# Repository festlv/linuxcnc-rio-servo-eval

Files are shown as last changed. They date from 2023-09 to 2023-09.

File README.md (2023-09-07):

# LinuxCNC-RIO evaluation/prototype board

This repository contains a quick&dirty board to evaluate feasibility of using [LinuxCNC-RIO](https://github.com/multigcs/LinuxCNC-RIO) for analog servo motor control.
The board is designed as an addon for [Colorlight i5](https://tomverbeure.github.io/2021/01/22/The-Colorlight-i5-as-FPGA-development-board.html) development board. 

Design contains:
* +/-10V analog output (from pwmdir input) + 24V enable output
* differential step/dir + single ended 24V enable output
* differential encoder input on DB9 connector (RS422) with index pulse. Pinout for Ditron DC10 linear scale.
* 4 single ended 24V inputs (limit switches, EStop)
* +24V input, +5V, +/- 15V outputs for development board and analog output.

__N.B.__: There is no isolation present on the board, it relies on the Ethernet isolation alone!

## Current state

The design is not verified in real hardware yet, proceed with caution. Some aspects of the design were simulated in LTSpice, see `ltspice/`

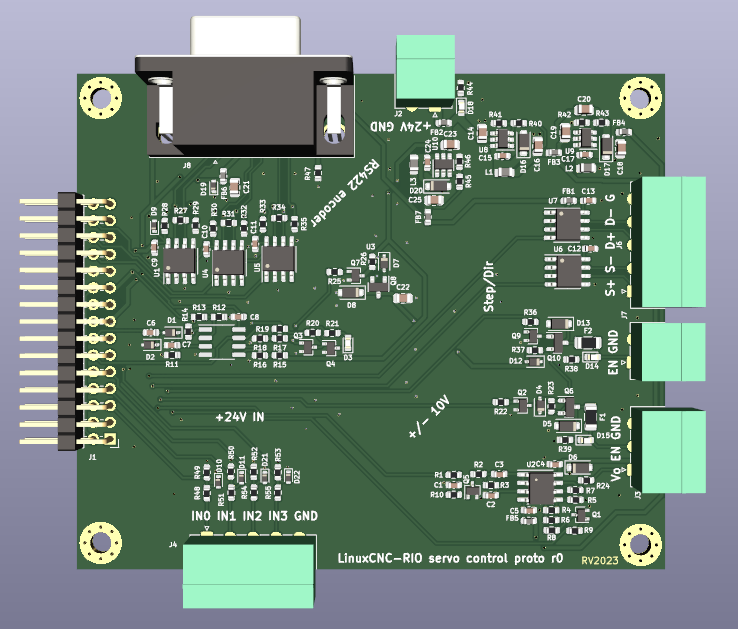
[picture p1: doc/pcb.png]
3d render of the pcb


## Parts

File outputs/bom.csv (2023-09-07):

Source: | /home/reinis/personal/cnc/colorlight-cnc-proto/colorlight-cnc-proto.kicad_sch
Date: | Thu 07 Sep 2023 10:59:34 AM EEST
Tool: | Eeschema 7.0.7
Generator: | /usr/share/kicad/plugins/bom_csv_grouped_by_value.py
Component Count: | 141
Collated Components:
Item | Qty | Reference(s) | Value | LibPart | Footprint | Datasheet | DNP | LCSC# | MPN | Manufacturer
1 | 1 | C1 | 3.3nF | Device:C_Small | Capacitor_SMD:C_0603_1608Metric | ~
2 | 1 | C2 | 220pF | Device:C_Small | Capacitor_SMD:C_0603_1608Metric | ~
3 | 1 | C3 | 680pF | Device:C_Small | Capacitor_SMD:C_0603_1608Metric | ~
4 | 12 | C4, C5, C6, C8, C9, C10, C11, C12, C13, C15, C17, C24 | 0.1uF | Device:C_Small | Capacitor_SMD:C_0603_1608Metric | ~
5 | 1 | C7 | 1uF | Device:C_Small | Capacitor_SMD:C_0603_1608Metric | ~
6 | 9 | C14, C16, C18, C19, C20, C21, C22, C23, C25 | 10uF | Device:C_Small | Capacitor_SMD:C_0805_2012Metric | ~ |  | C440198 | GRM21BR61H106KE43L
7 | 2 | D1, D2 | BAT54WS | hadv-diodes:BAT54WS | Diode_SMD:D_SOD-323 | https://datasheet.lcsc.com/lcsc/2206271801_FUXINSEMI-BAT54WS_C3040452.pdf |  | C3040452 | BAT54WS | Fuxinsemi
8 | 3 | D3, D14, D15 | LED_RED | hadv-ui:LED_RED | LED_SMD:LED_0603_1608Metric | ~ |  | C434419 | SZYY0603R | Yongyu Photoelectric
9 | 3 | D4, D7, D12 | BZT52C10S | hadv-diodes:BZT52C10S | Diode_SMD:D_SOD-323 | ~ |  | C5270769 | BZT52C10S | YFW
10 | 3 | D5, D8, D13 | SMF24A | hadv-protection:SMF24A | Diode_SMD:D_SOD-123F | https://datasheet.lcsc.com/lcsc/2304140030_Shandong-Jingdao-Microelectronics-SMF24A_C169430.pdf |  | C169430 | SMF24A | Shandong Jingdao Microelectronics
11 | 1 | D6 | SMF10CA | hadv-protection:SMF10CA | Diode_SMD:D_SOD-123F | https://www.littelfuse.com/~/media/electronics/datasheets/tvs_diode_arrays/littelfuse_tvs_diode_array_sd_c_datasheet.pdf.pdf |  | C5310922 | SMF10CA | Sunmate
12 | 5 | D9, D10, D11, D21, D22 | BSD5C031V | hadv-protection:BSD5C031V | Diode_SMD:D_SOD-523 | https://datasheet.lcsc.com/lcsc/1912111437_BORN-BSD5C031V_C151984.pdf |  | C151984 | BSD5C031V | BORN
13 | 3 | D16, D17, D20 | DSS34 | hadv-diodes:DSS34 | Diode_SMD:D_SOD-123F | https://datasheet.lcsc.com/lcsc/2004141809_BORN-DSS34_C511866.pdf |  | C511866 | DSS34 | BORN
14 | 1 | D18 | LED_GREEN | hadv-ui:LED_GREEN | LED_SMD:LED_0603_1608Metric | ~ |  | C434423 | SZYY0603YG | Yongyu Photoelectric
15 | 1 | D19 | PESD5V0S1BBN | hadv-protection:PESD5V0S1BBN | Diode_SMD:D_SOD-523 | https://datasheet.lcsc.com/lcsc/1912111437_BORN-PESD5V0S1BBN_C314264.pdf |  | C314264 | PESD5V0S1BBN | BORN
16 | 2 | F1, F2 | BSMD1206-100-24V | hadv-protection:BSMD1206-100-24V | Fuse:Fuse_1206_3216Metric | ~ |  | C910830 | BSMD1206-100-24V | BHFUSE
17 | 7 | FB1, FB2, FB3, FB4, FB5, FB6, FB7 | FB_100R_3A | hadv-passives:FB_100R_3A | Inductor_SMD:L_0603_1608Metric | ~ |  | C96995 | UPZ1608E101-3R0TF | Sunlord
18 | 1 | J1 | Conn_02x15_Odd_Even | Connector_Generic:Conn_02x15_Odd_Even | Connector_PinHeader_2.54mm:PinHeader_2x15_P2.54mm_Horizontal | ~ |  | C2894995
19 | 2 | J2, J7 | TERM-BLK-2H | hadv-connectors:TERM-BLK-2H | Connector_Phoenix_MC:PhoenixContact_MC_1,5_2-G-3.5_1x02_P3.50mm_Horizontal | ~ |  | C441171 | KF2EDGR-3.5-2P | Cixi Kefa Elec
20 | 1 | J3 | TERM-BLK-3H | hadv-connectors:TERM-BLK-3H | Connector_Phoenix_MC:PhoenixContact_MC_1,5_3-G-3.5_1x03_P3.50mm_Horizontal | ~ |  | C441172 | KF2EDGR-3.5-3P | Cixi Kefa Elec
21 | 2 | J4, J6 | TERM-BLK-5H | hadv-connectors:TERM-BLK-5H | Connector_Phoenix_MC:PhoenixContact_MC_1,5_5-G-3.5_1x05_P3.50mm_Horizontal | ~ |  | C441174 | KF2EDGR-3.5-5P | Cixi Kefa Elec
22 | 1 | J8 | DB9_Receptacle | hadv-connectors:DB9_Receptacle | Connector_Dsub:DSUB-9_Female_Horizontal_P2.77x2.84mm_EdgePinOffset7.70mm_Housed_MountingHolesOffset9.12mm | ~ |  | C141882 | D-DMR009PF-D002 | Ckmtw
23 | 3 | L1, L2, L3 | MLP2012S4R7MT0S1 | hadv-inductors:MLP2012S4R7MT0S1 | Inductor_SMD:L_0805_2012Metric | ~ |  | C87543 | MLP2012S4R7MT0S1 | TDK
24 | 7 | Q1, Q2, Q3, Q4, Q5, Q7, Q9 | BSS138W | hadv-transistors:BSS138W | Package_TO_SOT_SMD:SOT-323_SC-70 | ~ |  | C504052 | BSS138W | Jiangsu Changjing Electronics Technology Co., Ltd.
25 | 3 | Q6, Q8, Q10 | AO3401A | hadv-transistors:AO3401A | Package_TO_SOT_SMD:SOT-23 | http://www.vishay.com/docs/70209/70209.pdf |  | C347476 | AO3401A | UMW
26 | 29 | R1, R4, R5, R6, R9, R10, R14, R15, R17, R18, R19, R20, R22, R23, R25, R26, R36, R37, R38, R39, R44, R48, R49, R50, R51, R52, R53, R54, R55 | 10K | Device:R_Small | Resistor_SMD:R_0603_1608Metric | ~
27 | 1 | R2 | 150K | Device:R_Small | Resistor_SMD:R_0603_1608Metric | ~
28 | 3 | R3, R11, R13 | 47K | Device:R_Small | Resistor_SMD:R_0603_1608Metric | ~
29 | 1 | R7 | 70K | Device:R_Small | Resistor_SMD:R_0603_1608Metric | ~
30 | 1 | R8 | 5.83K | Device:R_Small | Resistor_SMD:R_0603_1608Metric | ~
31 | 1 | R12 | 100K | Device:R_Small | Resistor_SMD:R_0603_1608Metric | ~
32 | 8 | R16, R21, R28, R29, R30, R32, R33, R35 | 1K | Device:R_Small | Resistor_SMD:R_0603_1608Metric | ~
33 | 1 | R24 | 10R | Device:R_Small | Resistor_SMD:R_0603_1608Metric | ~
34 | 3 | R27, R31, R34 | 120R | Device:R_Small | Resistor_SMD:R_0603_1608Metric | ~
35 | 2 | R40, R42 | 510K | Device:R_Small | Resistor_SMD:R_0603_1608Metric | ~
36 | 2 | R41, R43 | 30K | Device:R_Small | Resistor_SMD:R_0603_1608Metric | ~
37 | 1 | R45 | 82K | Device:R_Small | Resistor_SMD:R_0603_1608Metric | ~
38 | 1 | R46 | 16K | Device:R_Small | Resistor_SMD:R_0603_1608Metric | ~
39 | 1 | R47 | 0R | Device:R_Small | Resistor_SMD:R_0603_1608Metric | ~
40 | 5 | U1, U4, U5, U6, U7 | CS48505S | hadv-interface:CS48505S | Package_SO:SOIC-8_3.9x4.9mm_P1.27mm | https://datasheet.lcsc.com/lcsc/2207041730_Chipanalog-CS48505S_C3202824.pdf |  | C3202824 | CS48505S | Chipanalog
41 | 1 | U2 | LM358DT | hadv-opamps:LM358DT | Package_SO:SO-8_3.9x4.9mm_P1.27mm | http://www.ti.com/lit/ds/symlink/lm2904-n.pdf |  | C9418 | LM358DT | STMicroelectronics
42 | 1 | U3 | LM2903 | hadv-opamps:LM393 | Package_SO:SOP-8_3.76x4.96mm_P1.27mm | http://www.ti.com/lit/ds/symlink/lm393.pdf |  | C400839 | LM393 | IDCHIP
43 | 3 | U8, U9, U10 | LGS5145 | hadv-vregs:LGS5145 | Package_TO_SOT_SMD:SOT-23-6 | https://datasheet.lcsc.com/lcsc/2304071600_Legend-Si-LGS5145_C5123971.pdf |  | C5123971 | LGS5145

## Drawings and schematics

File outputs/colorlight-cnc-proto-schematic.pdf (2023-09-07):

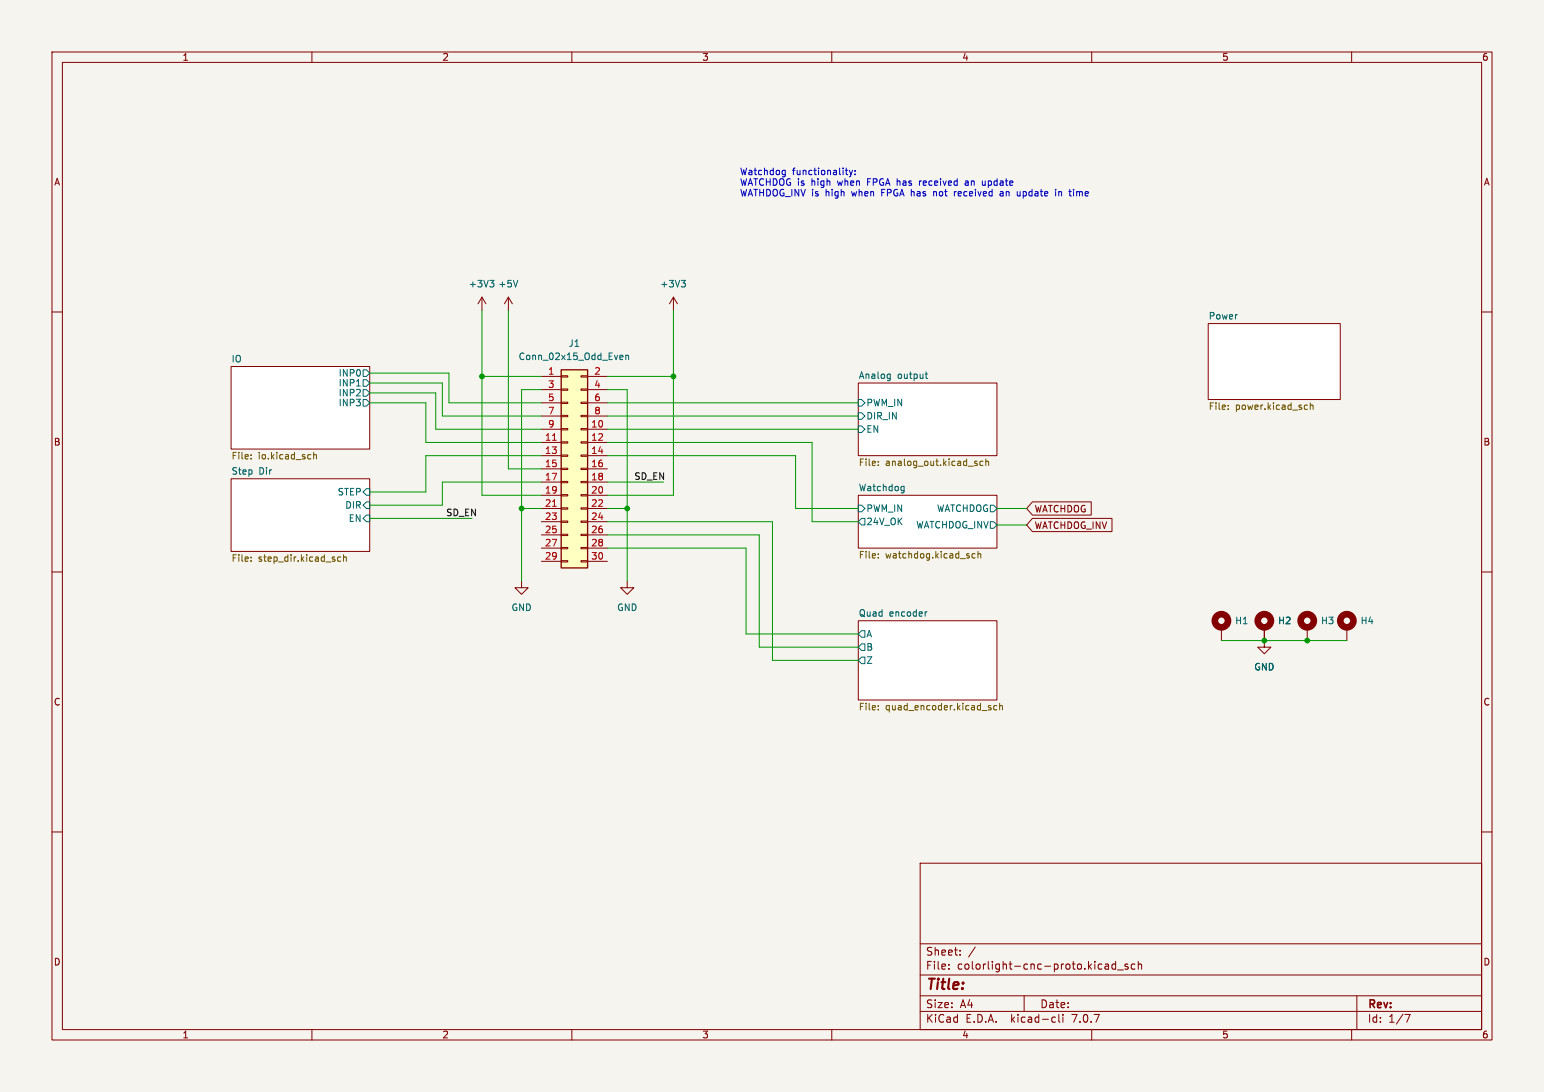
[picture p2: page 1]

9 | | 10
11 | | 12
13 | | 14

Id: 1/7 Title: File: colorlight-cnc-proto.kicad_sch Sheet: /

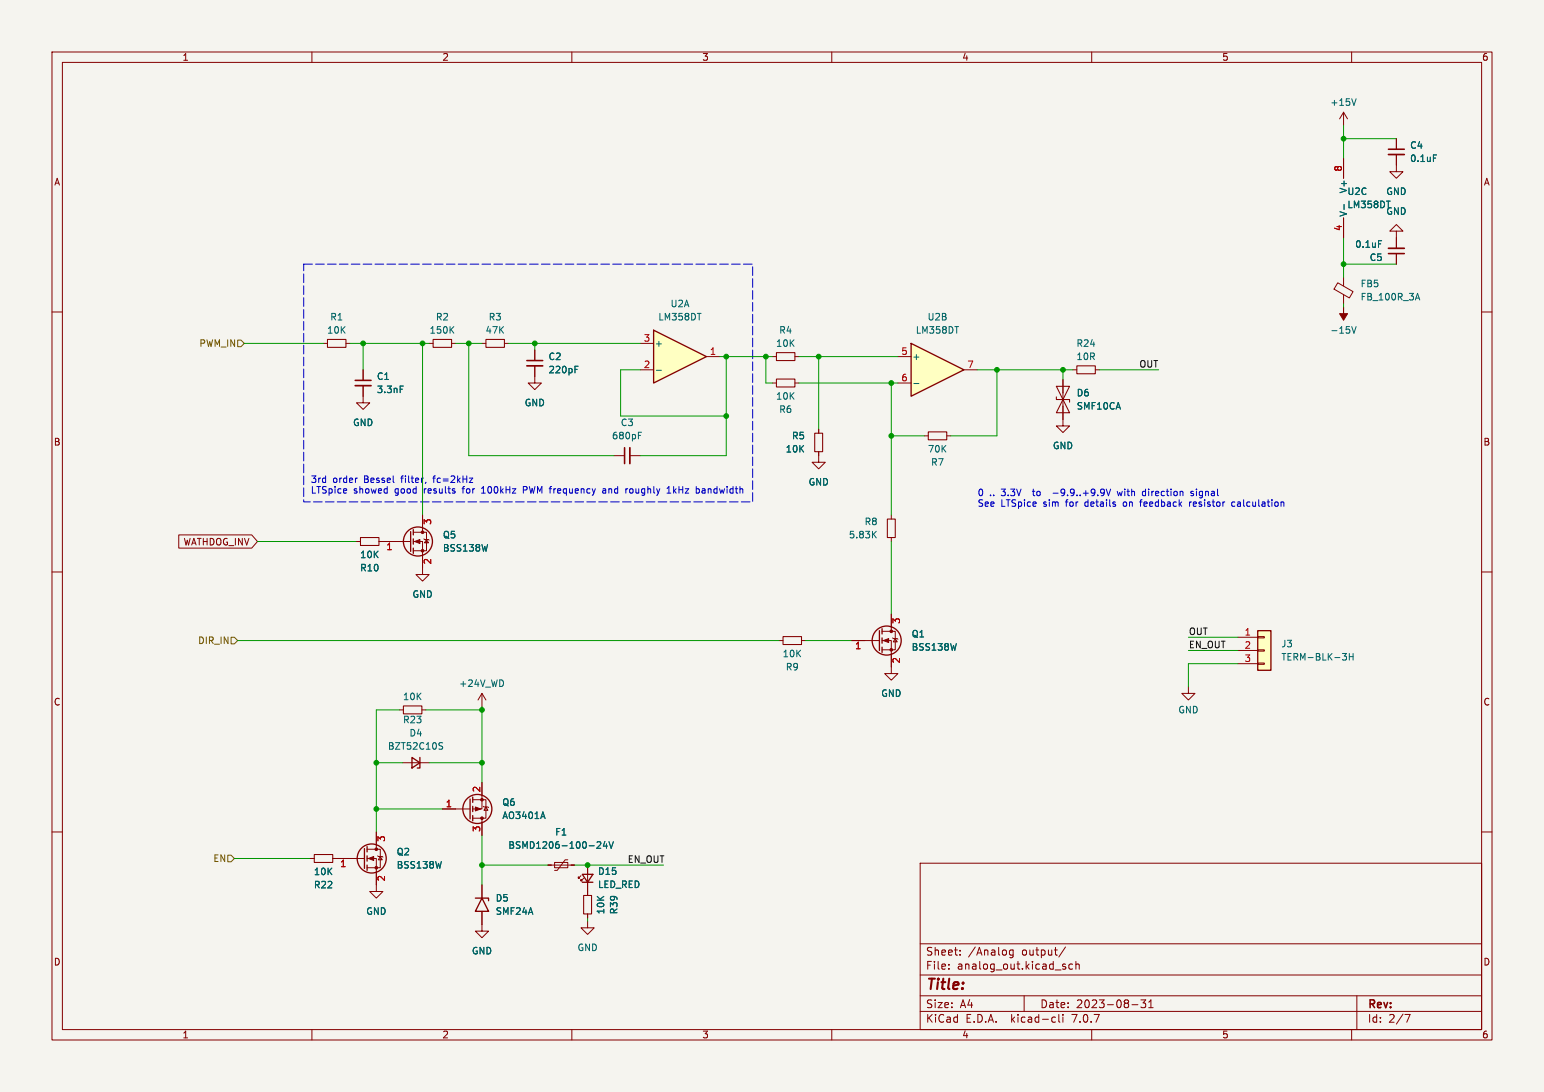
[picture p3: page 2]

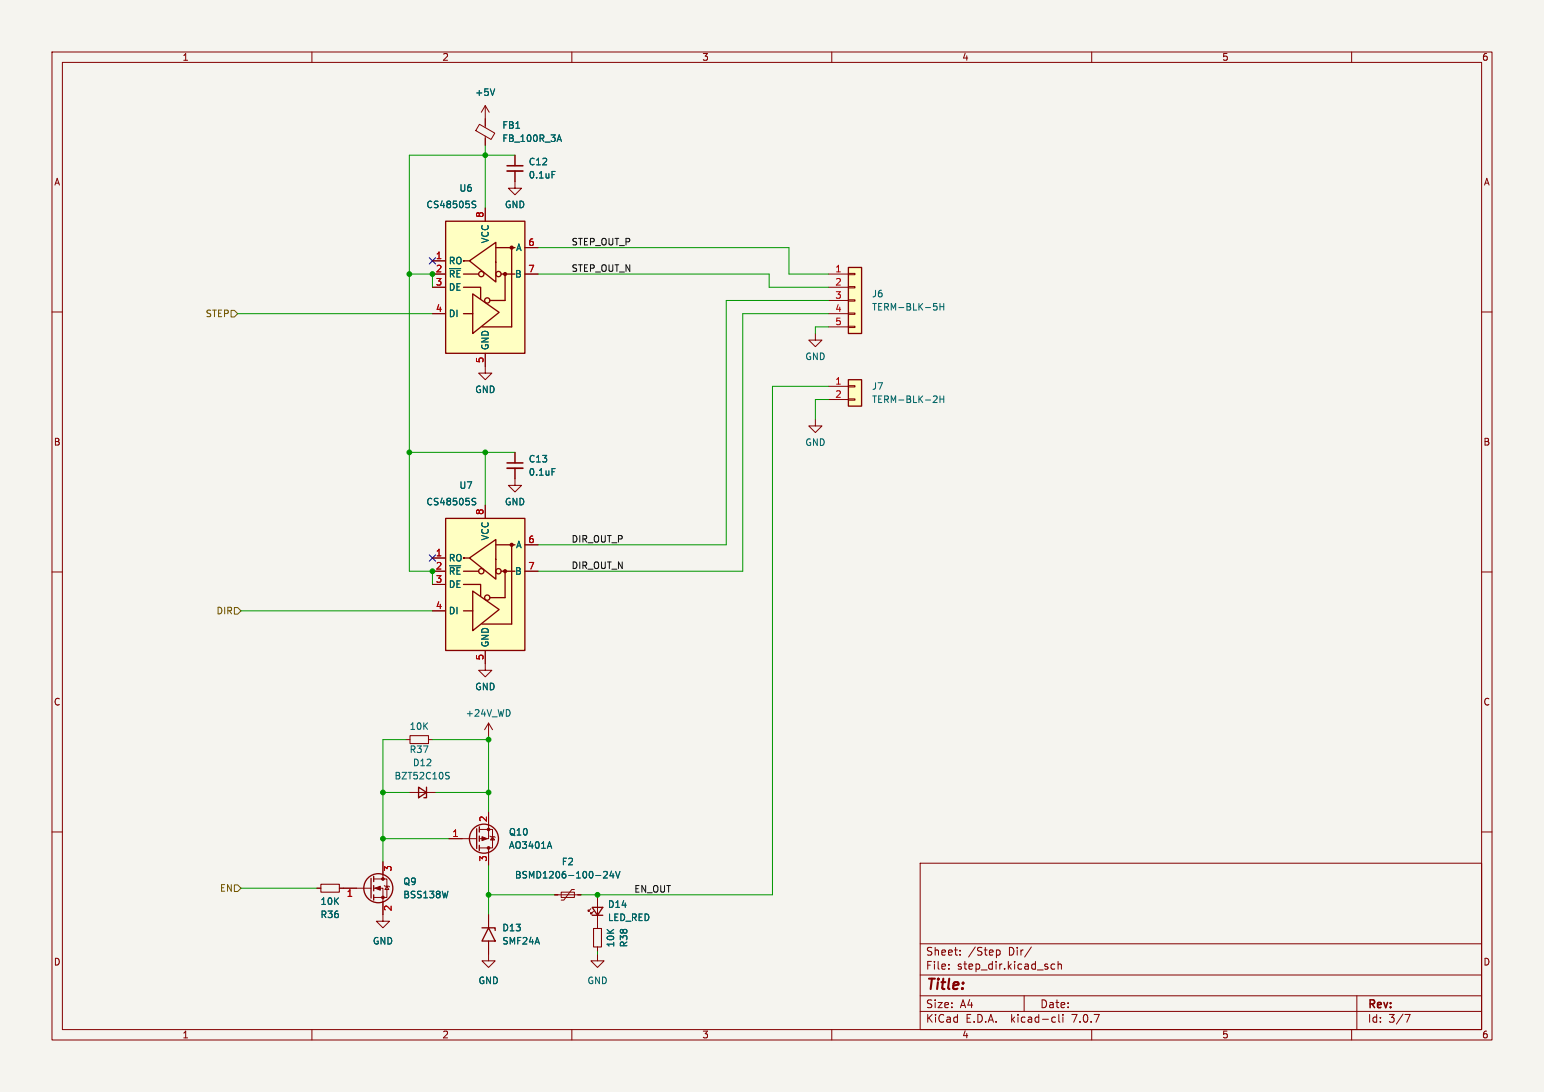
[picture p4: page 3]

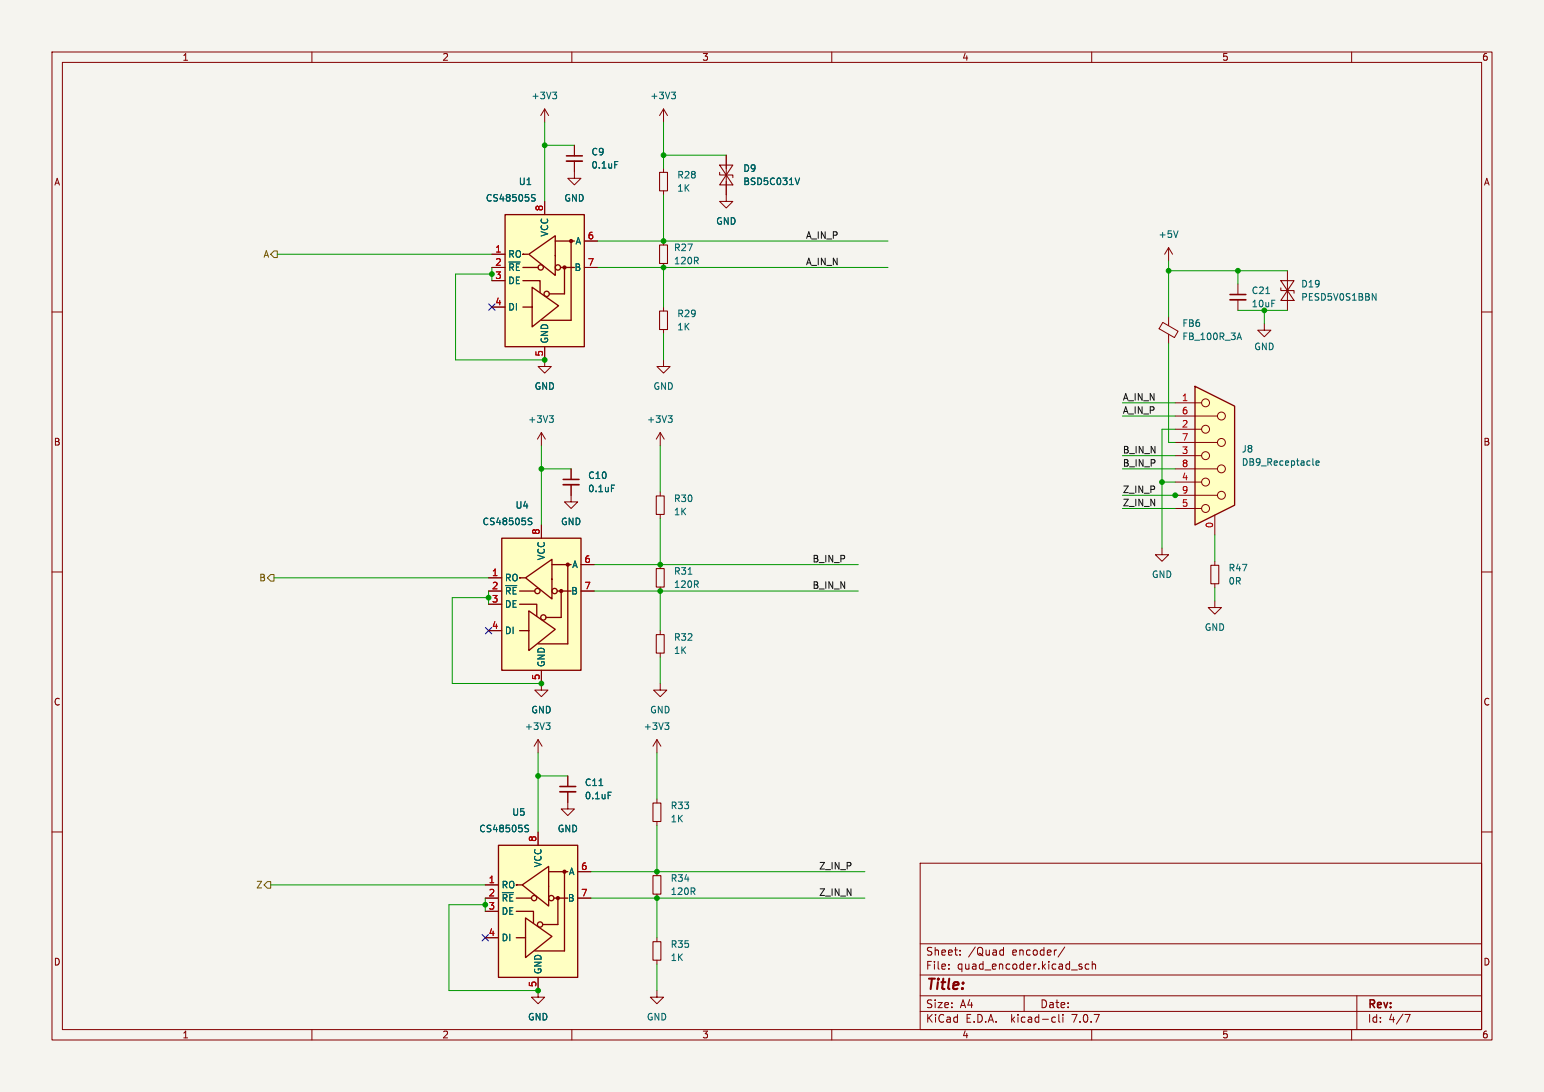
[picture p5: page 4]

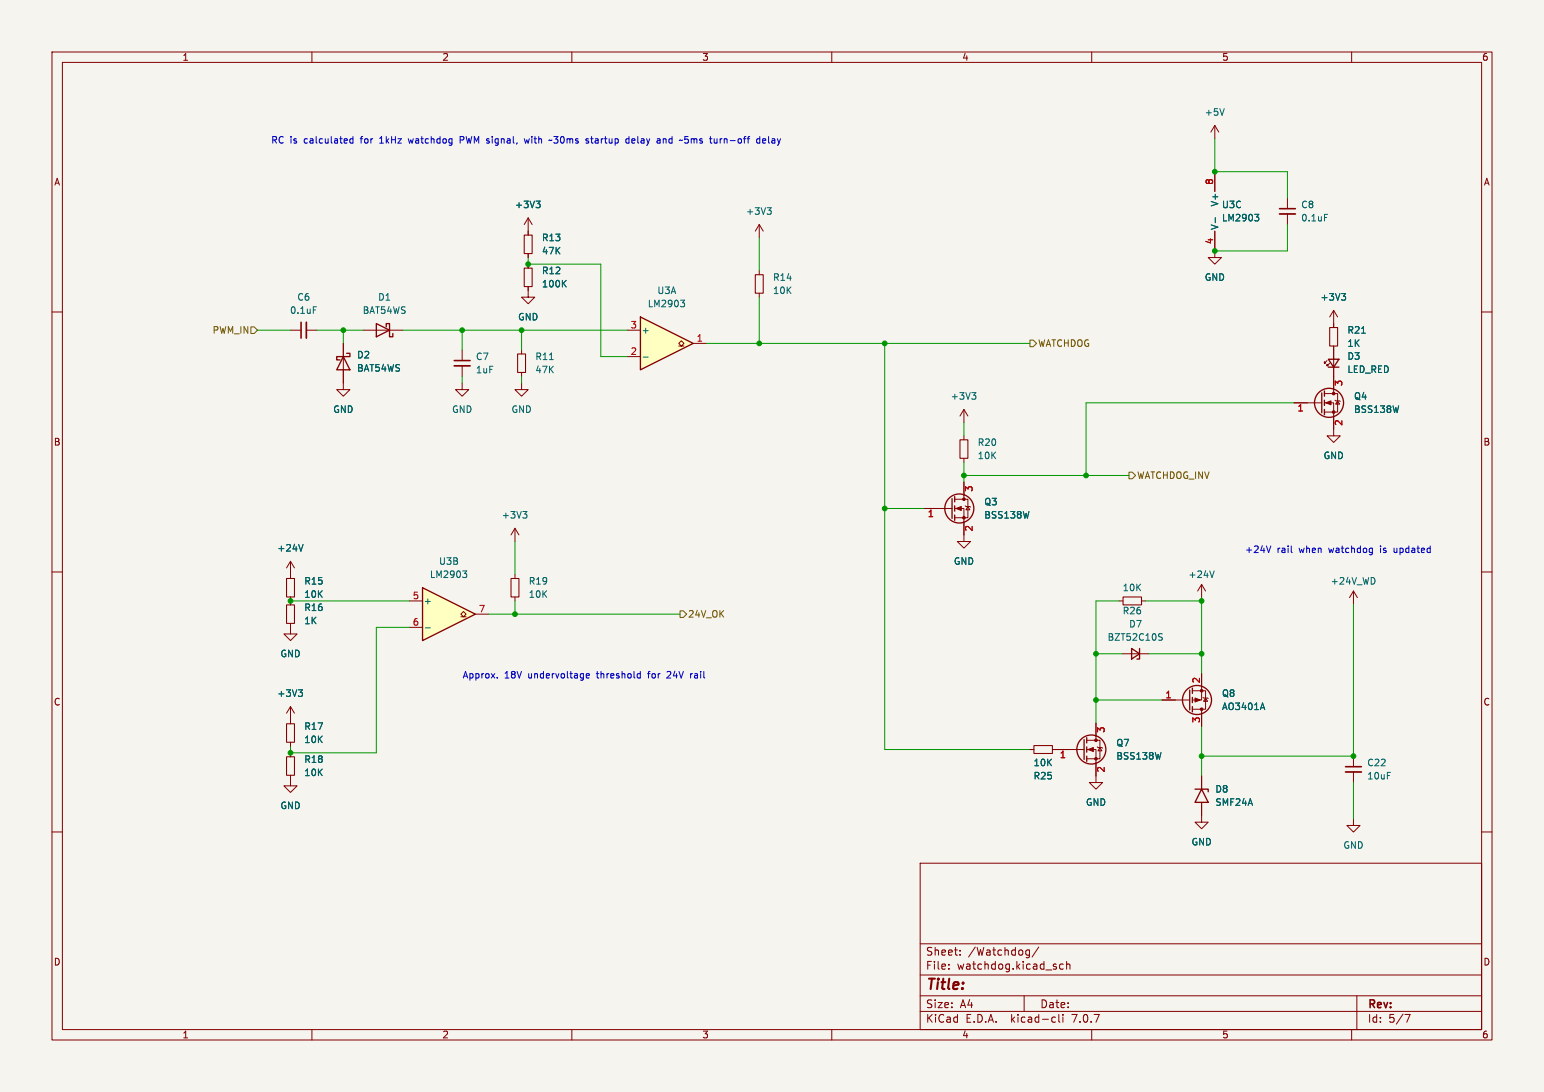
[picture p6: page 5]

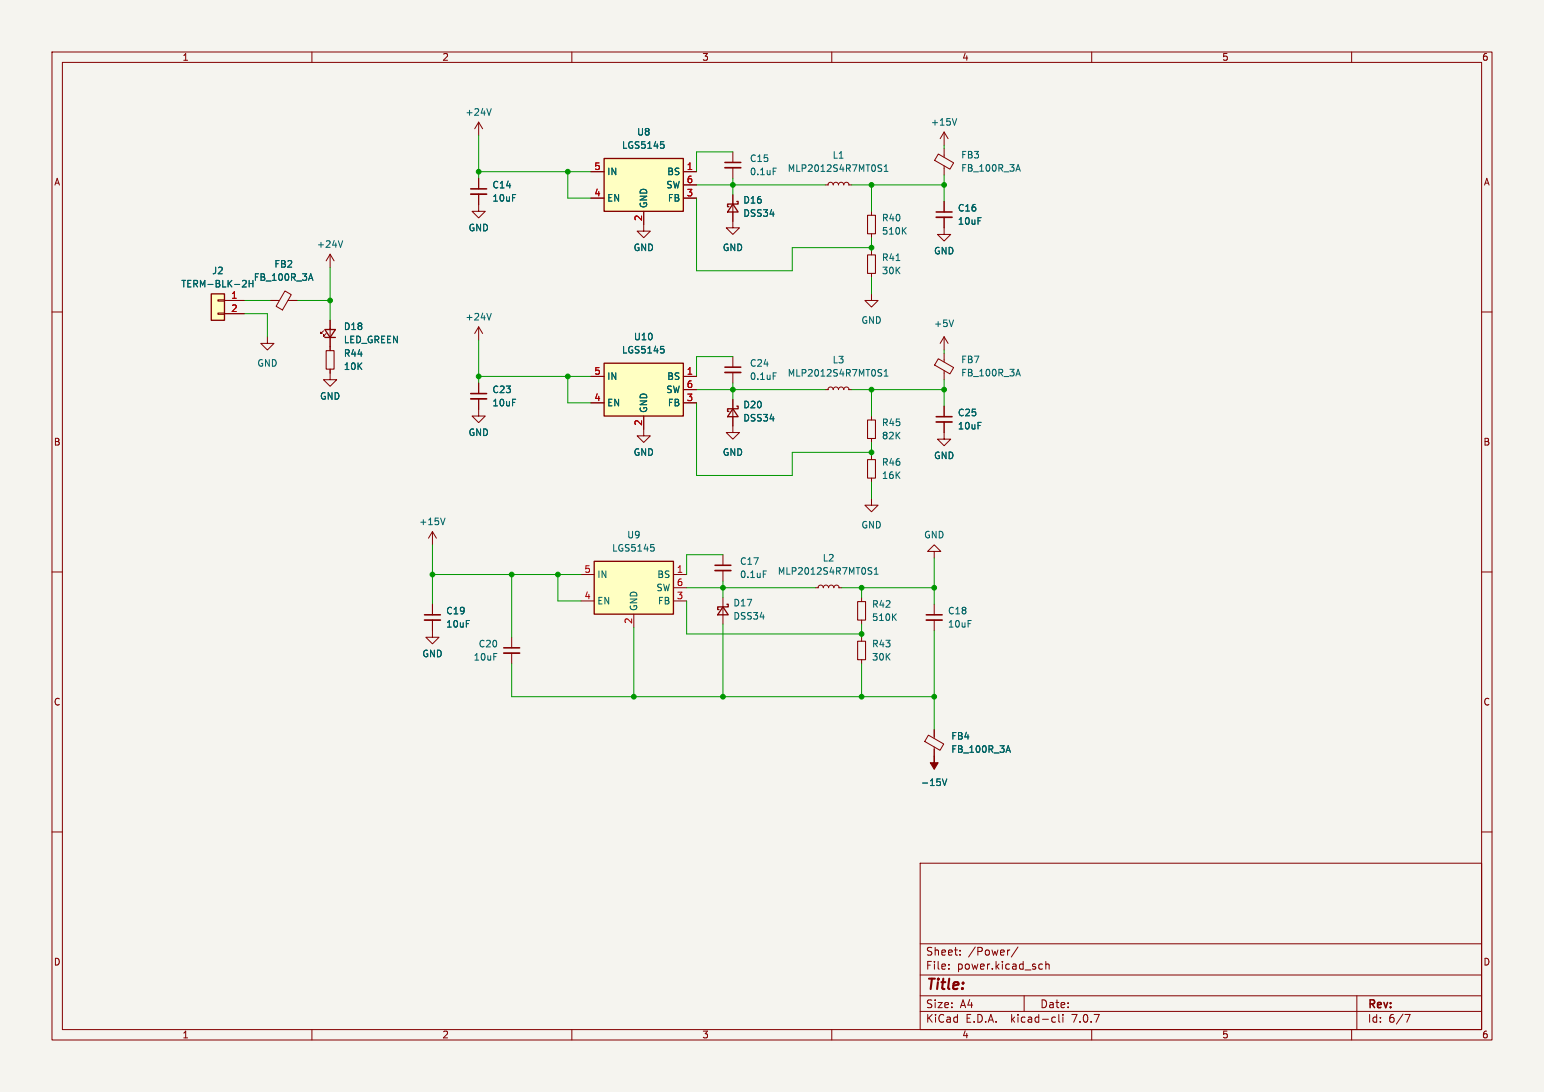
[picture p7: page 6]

Id: 6/7 Title: File: power.kicad_sch Sheet: /Power/

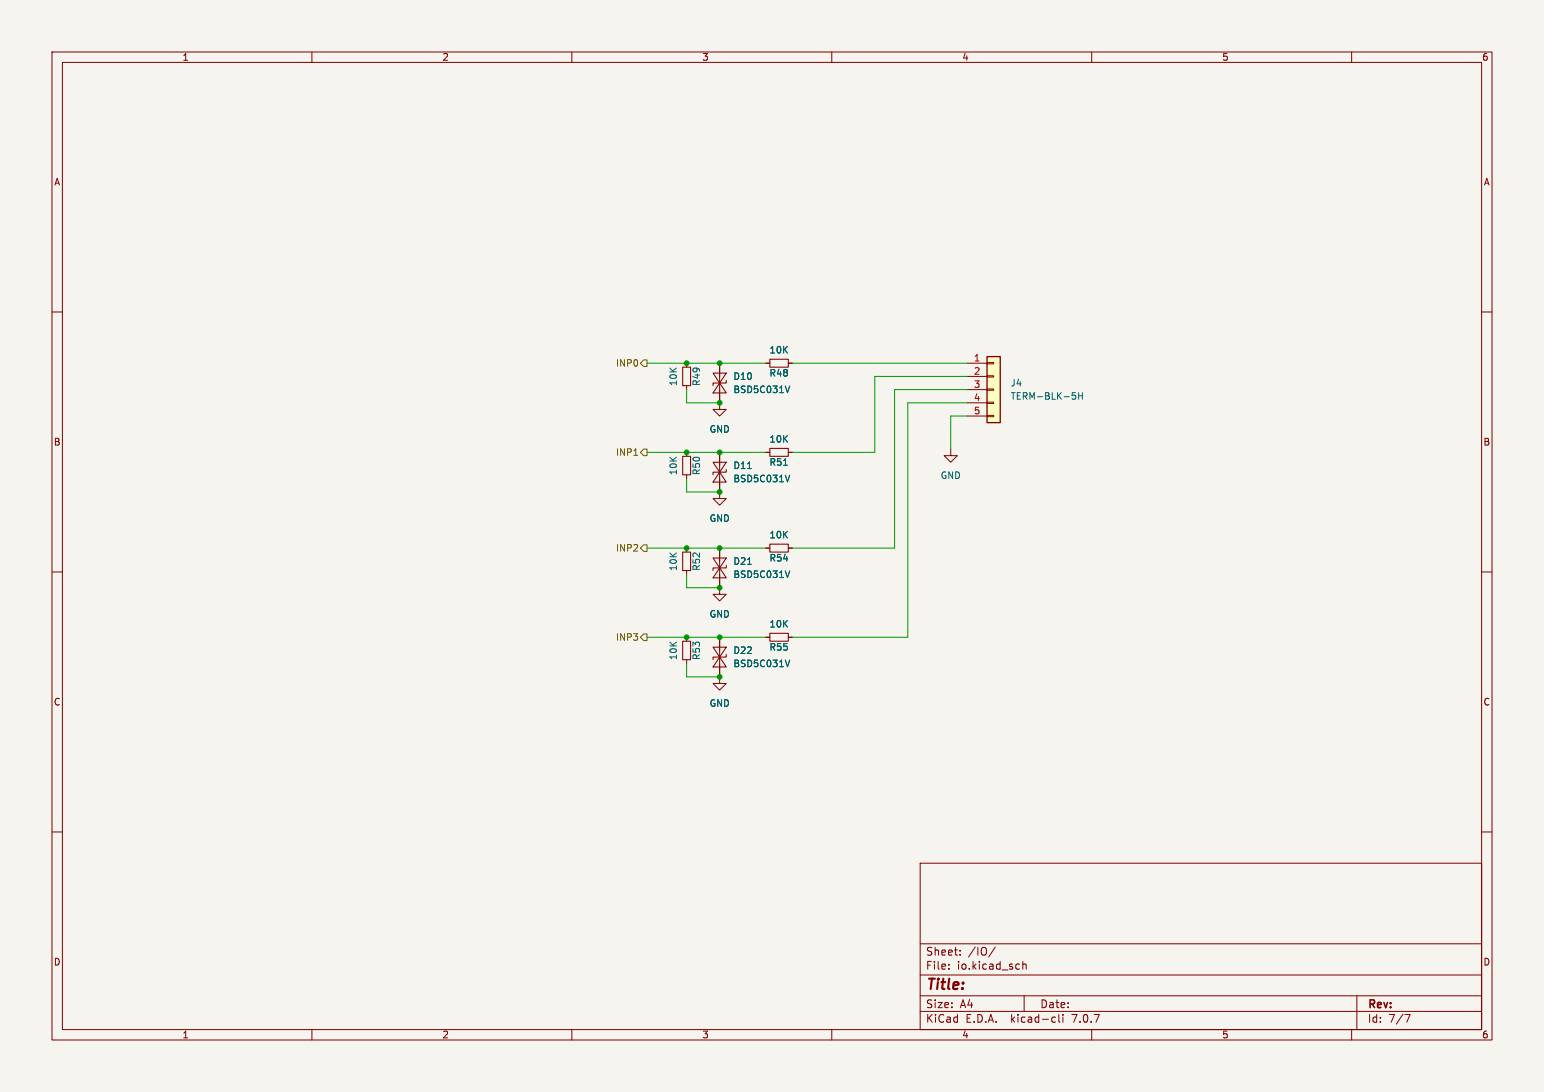
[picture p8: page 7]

Id: 7/7 Title: File: io.kicad_sch Sheet: /IO/

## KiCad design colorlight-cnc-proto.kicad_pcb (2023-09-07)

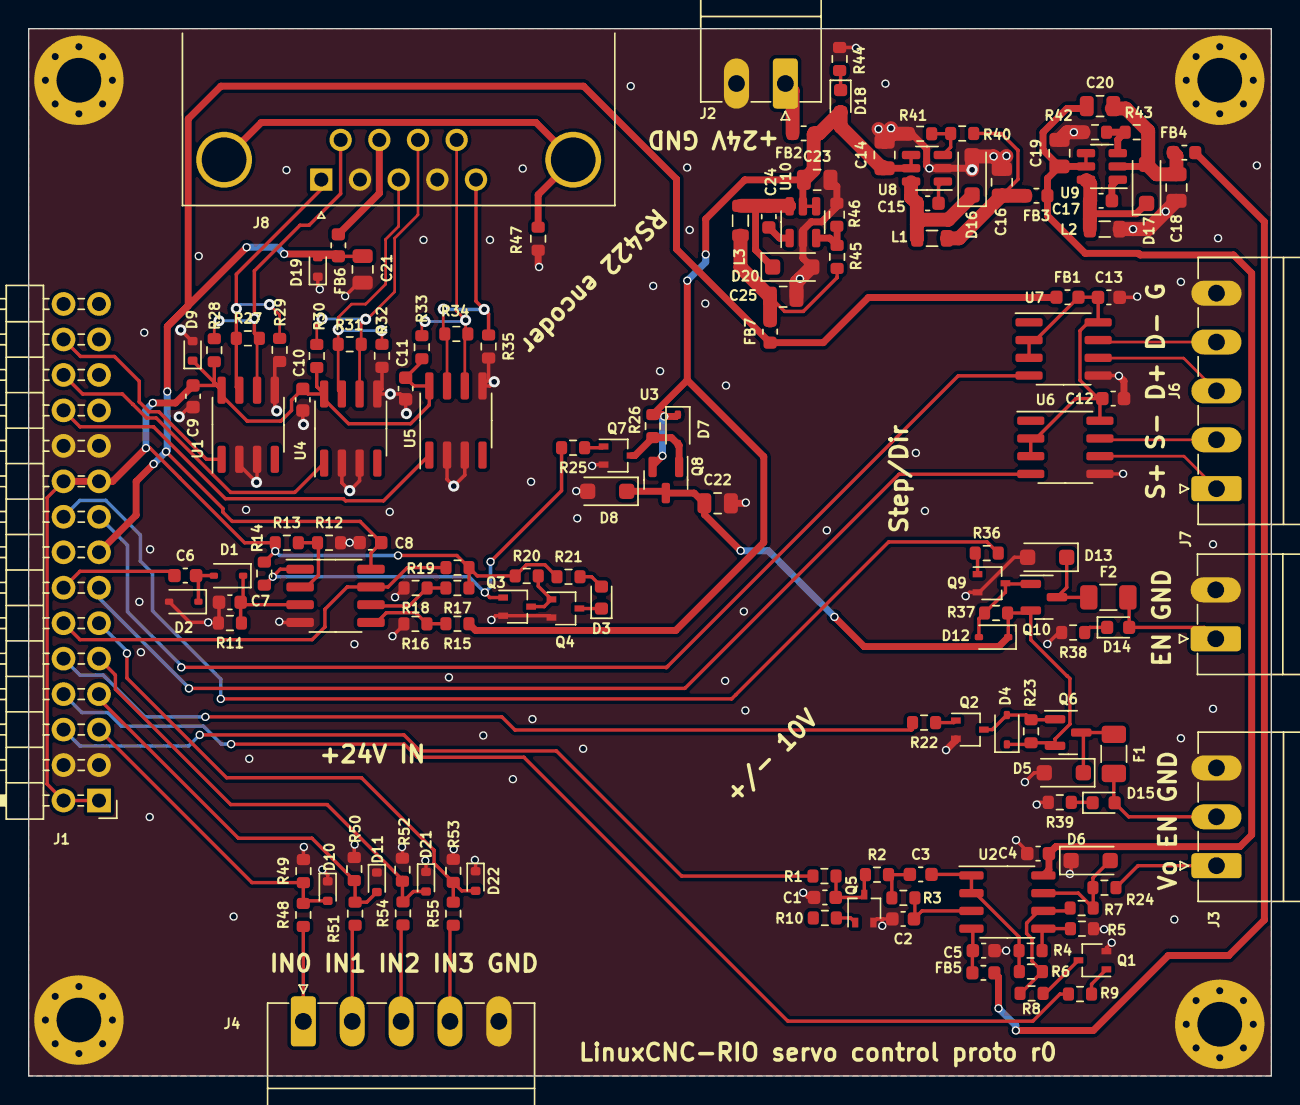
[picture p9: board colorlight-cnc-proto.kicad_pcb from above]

Board: 2 copper layers, 89.0 x 75.0 mm, 145 parts (0 on the bottom side), 86 nets.

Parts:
C1: 3.3nF; C_0603_1608Metric
C2: 220pF; C_0603_1608Metric
C3: 680pF; C_0603_1608Metric
C4, C5, C6, C8, C9, C10, C11, C12, C13, C15, C17, C24: 0.1uF; C_0603_1608Metric
C7: 1uF; C_0603_1608Metric
C14, C16, C18, C19, C20, C21, C22, C23, C25: 10uF; C_0805_2012Metric
D1, D2: BAT54WS; D_SOD-323
D3, D14, D15: LED_RED; LED_0603_1608Metric
D4, D7, D12: BZT52C10S; D_SOD-323
D5, D8, D13: SMF24A; D_SOD-123F
D6: SMF10CA; D_SOD-123F
D9, D10, D11, D21, D22: BSD5C031V; D_SOD-523
D16, D17, D20: DSS34; D_SOD-123F
D18: LED_GREEN; LED_0603_1608Metric
D19: PESD5V0S1BBN; D_SOD-523
F1, F2: BSMD1206-100-24V; Fuse_1206_3216Metric
FB1, FB2, FB3, FB4, FB5, FB6, FB7: FB_100R_3A; L_0603_1608Metric
H1, H2, H3, H4: MH_3.2mm; MountingHole_3.2mm_M3_Pad_Via
J1: Conn_02x15_Odd_Even; PinHeader_2x15_P2.54mm_Horizontal
J2, J7: TERM-BLK-2H; PhoenixContact_MC_1,5_2-G-3.5_1x02_P3.50mm_Horizontal
J3: TERM-BLK-3H; PhoenixContact_MC_1,5_3-G-3.5_1x03_P3.50mm_Horizontal
J4, J6: TERM-BLK-5H; PhoenixContact_MC_1,5_5-G-3.5_1x05_P3.50mm_Horizontal
J8: DB9_Receptacle; DSUB-9_Female_Horizontal_P2.77x2.84mm_EdgePinOffset7.70mm_H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
L1, L2, L3: MLP2012S4R7MT0S1; L_0805_2012Metric
Q1, Q2, Q3, Q4, Q5, Q7, Q9: BSS138W; SOT-323_SC-70
Q6, Q8, Q10: AO3401A; SOT-23
R1, R4, R5, R6, R9, R10, R14, R15, R17, R18, R19, R20, R22, R23, R25, R26, R36, R37, R38, R39, R44, R48, R49, R50, R51, R52, R53, R54, R55: 10K; R_0603_1608Metric
R2: 150K; R_0603_1608Metric
R3, R11, R13: 47K; R_0603_1608Metric
R7: 70K; R_0603_1608Metric
R8: 5.83K; R_0603_1608Metric
R12: 100K; R_0603_1608Metric
R16, R21, R28, R29, R30, R32, R33, R35: 1K; R_0603_1608Metric
R24: 10R; R_0603_1608Metric
R27, R31, R34: 120R; R_0603_1608Metric
R40, R42: 510K; R_0603_1608Metric
R41, R43: 30K; R_0603_1608Metric
R45: 82K; R_0603_1608Metric
R46: 16K; R_0603_1608Metric
R47: 0R; R_0603_1608Metric
U1, U4, U5, U6, U7: CS48505S; SOIC-8_3.9x4.9mm_P1.27mm
U2: LM358DT; SO-8_3.9x4.9mm_P1.27mm
U3: LM2903; SOP-8_3.76x4.96mm_P1.27mm
U8, U9, U10: LGS5145; SOT-23-6

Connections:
+3V3: C9.1, C10.1, C11.1, D9.1 (A1), J1.1, J1.2, J1.19, J1.20, R13.1, R14.1, R17.1, R19.1, R20.1, R21.1, R28.1, R30.1, R33.1, U1.8 (VCC), U4.8 (VCC), U5.8 (VCC)
+5V: C8.1, C21.1, D19.2 (A2), FB1.1, FB6.1, FB7.1, J1.15, U3.8 (V+)
+15V: C4.1, C19.1, C20.1, FB3.1, U2.8 (V+), U9.4 (EN), U9.5 (IN)
+24V: C14.1, C23.1, D7.1 (K), D18.2 (A), FB2.2, Q8.2 (S), R15.1, R26.1, U8.4 (EN), U8.5 (IN), U10.4 (EN), U10.5 (IN)
+24V_WD: C22.1, D4.1 (K), D8.1 (A1), D12.1 (K), Q6.2 (S), Q8.3 (D), Q10.2 (S), R23.1, R37.1
-15V: FB4.2, FB5.2
/Analog output/DIR_IN: J1.8, R9.2
/Analog output/EN: J1.10, R22.2
/Analog output/EN_OUT: D15.2 (A), F1.2, J3.2
/Analog output/OUT: J3.1, R24.2
/Analog output/PWM_IN: J1.6, R1.1
/IO/INP0: D10.2 (A2), J1.5, R48.2, R49.1
/IO/INP1: D11.2 (A2), J1.7, R50.1, R51.2
/IO/INP2: D21.2 (A2), J1.9, R52.1, R54.2
/IO/INP3: D22.2 (A2), J1.11, R53.1, R55.2
/Quad encoder/A: J1.28, U1.1 (RO)
/Quad encoder/A_IN_N: J8.1, R27.1, R29.1, U1.7 (B)
/Quad encoder/A_IN_P: J8.6, R27.2, R28.2, U1.6 (A)
/Quad encoder/B: J1.26, U4.1 (RO)
/Quad encoder/B_IN_N: J8.3, R31.2, R32.1, U4.7 (B)
/Quad encoder/B_IN_P: J8.8, R30.2, R31.1, U4.6 (A)
/Quad encoder/Z: J1.24, U5.1 (RO)
/Quad encoder/Z_IN_N: J8.5, R34.2, R35.1, U5.7 (B)
/Quad encoder/Z_IN_P: J8.9, R33.2, R34.1, U5.6 (A)
/SD_EN: J1.18, R36.2
/Step Dir/DIR: J1.17, U7.4 (DI)
/Step Dir/DIR_OUT_N: J6.4, U7.7 (B)
/Step Dir/DIR_OUT_P: J6.3, U7.6 (A)
/Step Dir/EN_OUT: D14.2 (A), F2.2, J7.1
/Step Dir/STEP: J1.13, U6.4 (DI)
/Step Dir/STEP_OUT_N: J6.2, U6.7 (B)
/Step Dir/STEP_OUT_P: J6.1, U6.6 (A)
/Watchdog/24V_OK: J1.12, R19.2, U3.7
/Watchdog/PWM_IN: C6.1, J1.14
GND: C1.2, C2.2, C4.2, C5.2, C7.2, C8.2, C9.2, C10.2, C11.2, C12.2, C13.2, C14.2, C16.2, C18.1, C19.2, C21.2, C22.2, C23.2, C25.2, D2.2 (A), D5.2 (A2), D6.1 (A1), D8.2 (A2), D9.2 (A2), D10.1 (A1), D11.1 (A1), D13.2 (A2), D16.2 (A), D19.1 (A1), D20.2 (A), D21.1 (A1), D22.1 (A1), H1.1, H2.1, H3.1, H4.1, J1.3, J1.4, J1.21, J1.22, J2.2, J3.3, J4.5, J6.5, J7.2, J8.2, J8.4, L2.2, Q1.2 (S), Q2.2 (S), Q3.2 (S), Q4.2 (S), Q5.2 (S), Q7.2 (S), Q9.2 (S), R5.1, R11.2, R12.2, R16.2, R18.2, R29.2, R32.2, R35.2, R38.2, R39.2, R41.2, R42.1, R44.2, R46.2, R47.2, R49.2, R50.2, R52.2, R53.2, U1.2 (~RE), U1.3 (DE), U1.5 (GND), U3.4 (V-), U4.2 (~RE), U4.3 (DE), U4.5 (GND), U5.2 (~RE), U5.3 (DE), U5.5 (GND), U6.5 (GND), U7.5 (GND), U8.2 (GND), U10.2 (GND)
unnamed: C3.1, R2.2, R3.1
unnamed: C16.1, FB3.2, L1.2, R40.1
unnamed: C25.1, FB7.2, L3.2, R45.1
unnamed: C6.2, D1.2 (A), D2.1 (K)
unnamed: C7.1, D1.1 (K), R11.1, U3.3 (+)
unnamed: D3.2 (A), R21.2
unnamed: D3.1 (K), Q4.3 (D)
unnamed: D4.2 (A), Q2.3 (D), Q6.1 (G), R23.2
unnamed: D5.1 (A1), F1.1, Q6.3 (D)
unnamed: D6.2 (A2), R7.1, R24.1, U2.7
unnamed: D7.2 (A), Q7.3 (D), Q8.1 (G), R26.2
unnamed: D12.2 (A), Q9.3 (D), Q10.1 (G), R37.2
unnamed: D13.1 (A1), F2.1, Q10.3 (D)
unnamed: D14.1 (K), R38.1
unnamed: D15.1 (K), R39.1
unnamed: C15.2, D16.1 (K), L1.1, U8.6 (SW)
unnamed: C18.2, C20.2, D17.2 (A), FB4.1, R43.2, U9.2 (GND)
unnamed: C17.2, D17.1 (K), L2.1, U9.6 (SW)
unnamed: D18.1 (K), R44.1
unnamed: C24.2, D20.1 (K), L3.1, U10.6 (SW)
unnamed: FB6.2, J8.7
unnamed: FB2.1, J2.1
unnamed: J4.1, R48.1
unnamed: J4.2, R51.1
unnamed: J4.3, R54.1
unnamed: J4.4, R55.1
unnamed: J8.0 (PAD), R47.1
unnamed: Q1.3 (D), R8.1
unnamed: Q1.1 (G), R9.1
unnamed: Q2.1 (G), R22.1
unnamed: C1.1, Q5.3 (D), R1.2, R2.1
unnamed: Q5.1 (G), R10.1
unnamed: Q7.1 (G), R25.1
unnamed: Q9.1 (G), R36.1
unnamed: C2.1, R3.2, U2.3 (+)
unnamed: C3.2, R4.1, R6.2, U2.1, U2.2 (-)
unnamed: R4.2, R5.2, U2.5 (+)
unnamed: R6.1, R7.2, R8.2, U2.6 (-)
unnamed: C5.1, FB5.1, U2.4 (V-)
unnamed: R12.1, R13.2, U3.2 (-)
unnamed: R15.2, R16.1, U3.5 (+)
unnamed: R17.2, R18.1, U3.6 (-)
unnamed: C12.1, C13.1, FB1.2, U6.2 (~RE), U6.3 (DE), U6.8 (VCC), U7.2 (~RE), U7.3 (DE), U7.8 (VCC)
unnamed: C15.1, U8.1 (BS)
unnamed: R40.2, R41.1, U8.3 (FB)
unnamed: C17.1, U9.1 (BS)
unnamed: R42.2, R43.1, U9.3 (FB)
unnamed: C24.1, U10.1 (BS)
unnamed: R45.2, R46.1, U10.3 (FB)
WATCHDOG: Q3.1 (G), R14.2, R25.2, U3.1
WATCHDOG_INV: Q3.3 (D), Q4.1 (G), R20.2
